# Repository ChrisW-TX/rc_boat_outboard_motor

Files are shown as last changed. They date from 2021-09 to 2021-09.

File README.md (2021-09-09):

rc_boat_outboard_motor

I originally started this journey early 2021 with the idea to create a robotic pool skimmer for the in-ground pool I have.  
From that I decided to build my own RC boat-like object because I enjoy that kind of thing and most rc boats are aimed at zooming around a large space or being little more than toys.
I purchased a reasonable priced brushed motor and esc and a new receiver for the RC car controller I already own (Hobby King).  
I ordered some u-joints and boat propellors and shafts off Amazon and got to work designing this thing.  I had just recently been enthralled with the Windwows app Openscad which is a script based 3D Design app which I find fascinating to use, especially the paramerization that allows you to easly adjust the geomoetry of your designs.

I started playing with shaft and motor placement, tried fixed shafts with multiple u-joints and then a flex shaft but wasn't happy with any of the results.  Also designed a couple different rudder configurations to go with all that.  Then I saw an outboard motor for sale on Amazon for rc boats and thought, sure, I can do that.  Had to order a couple of bevel gears and some bearings but what's a few more parts and pieces in the name of R&D.
My thoughts were an outboard made sense because it simplifies the drive shaft setup and serves as a rudder at the same time.  I did play with some plastic bevel gears in a mock up.  I'm not sure how long they would last but they certainly work.  

I started creating all my models in Openscad for Windows but switched to using Shapr3D on an iPad pro around April 2021 and other than going back to Openscad for some screw thread generation, it's been great.  I've always struggled with 3D design in the past using SketchUp and others but Shapr3D is very intuitive with the Apple pencil. 

I had just recently treated myself to a new iPad Pro so I could play with Shapr3D, which promises a new experience in 3D design, something I have struggled with in the past.

So I based this design on a mockup I did of the parts that I had:

Turnigy Trackstar 540-20T Brushed Motor (36mm diameter).  
	This only has an RPM rating of 11,700 but I wanted a high torque motor for power over speed.
One 100mm long 4mm boat prop shaft (threaded on one end) with a 50mm Barrel you fill with grease.
One 105mm long 4mm shaft I had cut from a longer one I originally bought. 
One 4mm to 3.175mm U-Joint coupler to connect the 105mm shaft to the motor I have.
Two BQLZR 15T 0.8 Module Tapered Bevel Gear Wheel 4mm Bore Diameter Yellow for Model Car from Amazon (no longer available, apparently)
One 4mm boat propellor collar from another boat prop shaft (Using as a collar on the inside of the prop shaft barrel).
Three 4mm ID x 15mm OD x 5mm Deep bearings (from Amazon)

I designed all the these parts in Shapr3D (except threads) in a 90 degree configuration and designed the housing around them.  
This is the second version of the housing as I wasn't happy with the first one at all and never tried to use it after I printed it.  It didn't seem very sturdy.

I admit this is far uglier than I wanted it to be and maybe I'll make it look more like an outboard motor in the future.  Right now I'm happy with how it works and I'm particularly proud of the screw adjustment to raise/lower the motor to adjust pressure on the bevel gear meshing.
I reused a steering horn extension I already had on my last working rudder that raises the connection point up to connect with the servo rod.  There are some holes I didn't add to the model that I ended up drilling by hand because I wasn't sure where I would ultimately want them.  The holes that match the ones in the outboard bracket were drilled once I determined the height I wanted it to sit on my boat.  I also added a single hole for a screw to lock the thread adjustment in place as the torque from the motor I'm using would easily spin it around.

I've included the Openscad file and .stl I used for the threads.  If you want to use those, you'll have to configure your Openscad libraries per that authors instructions: https://github.com/adrianschlatter/threadlib
I just played around with the standard thread sizes available to find one that my motor would fit inside of with some wriggle room.  Also wanted a relatively thick and hearty thread size to make it easier to use in plastic.

I've printed all my 3d stuff in PETG because it's more durable in extreme environments such as weather, water and sunlight.  I printed all of this on my Prusa MK3S+ with a .06 nozzle which greatly reduces print times.  Even then this whole thing was over 16 hours, printing with "supports everywhere".

One thing I will be adding for sure is a cover for the motor so it has less chance to get wet.  This will be a good opportunity to give it more of an "outboard" motor shape.

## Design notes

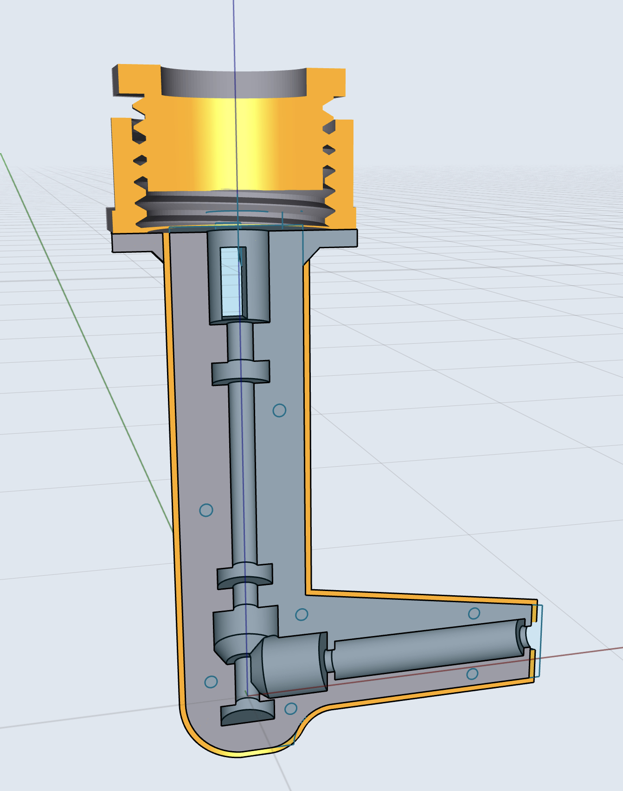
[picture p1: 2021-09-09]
X-ray view.jpg

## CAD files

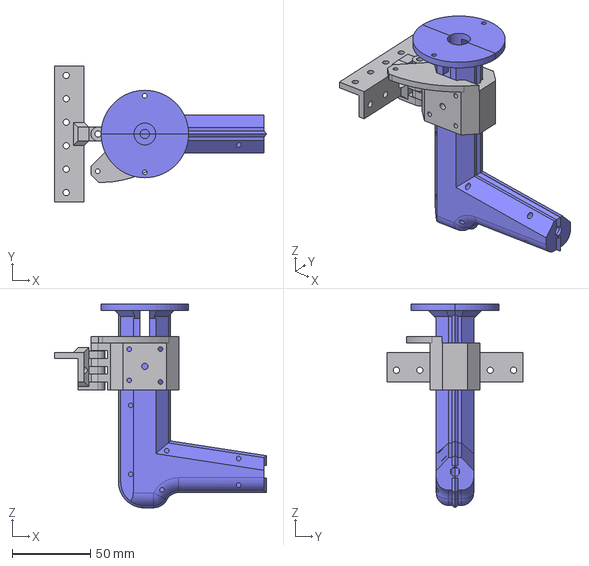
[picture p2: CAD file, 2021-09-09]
Outboard v2.step
135.6 x 87.0 x 130.3 mm

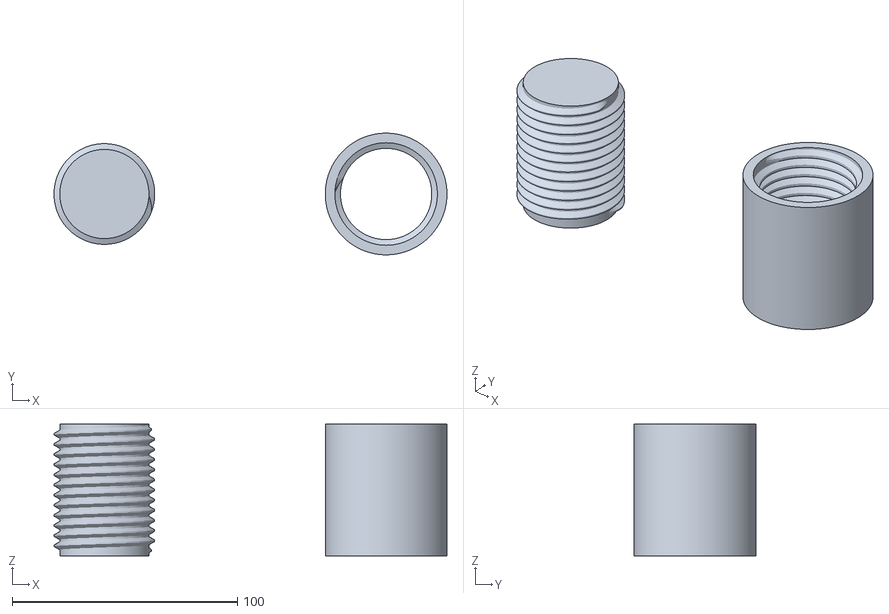
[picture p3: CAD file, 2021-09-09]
ThreadLib-M45 Screw and Nut.stl
174.3 x 54.0 x 58.5

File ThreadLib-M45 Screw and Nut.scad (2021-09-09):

$fn=100;
use <threadlib/threadlib.scad>

//translate([0, 100, 0])
//cylinder(h=15, r=16.15, center=true);

difference() {
    union() {
        //translate([0, 0, 13])
            //cylinder(h=4, r=15, $fn=6);
        bolt("M45", turns=12);
    }
    //cylinder(h=140, r=16.15, center=true);
}

translate([125, 0, 0])
    union() {
        //difference() {
        //    cylinder(h=25, r=18.15, center=false);
        //    cylinder(h=140, r=16.15, center=true); }
        nut("M45", turns=12, Douter=54);
        //translate([0, 0, 18.5])
            //cylinder(h=4, r=15, $fn=6);
}

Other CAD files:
Outboard v2.stl

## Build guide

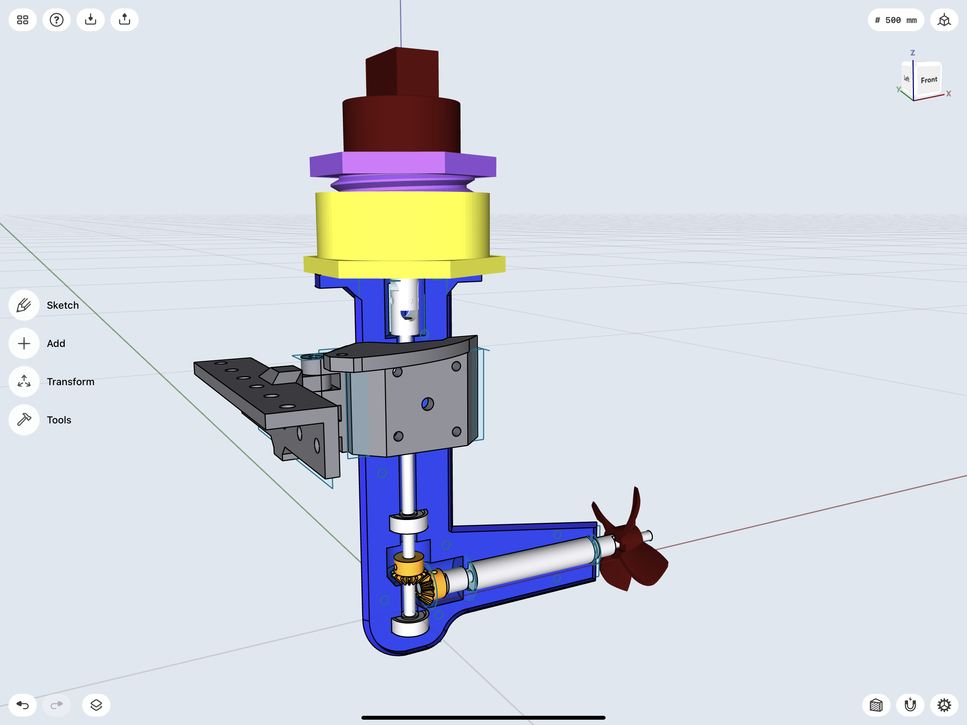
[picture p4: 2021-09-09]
Complete Assembly minus left side.PNG
